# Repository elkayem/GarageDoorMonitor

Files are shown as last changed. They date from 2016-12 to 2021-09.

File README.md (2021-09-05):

# GarageDoorMonitor

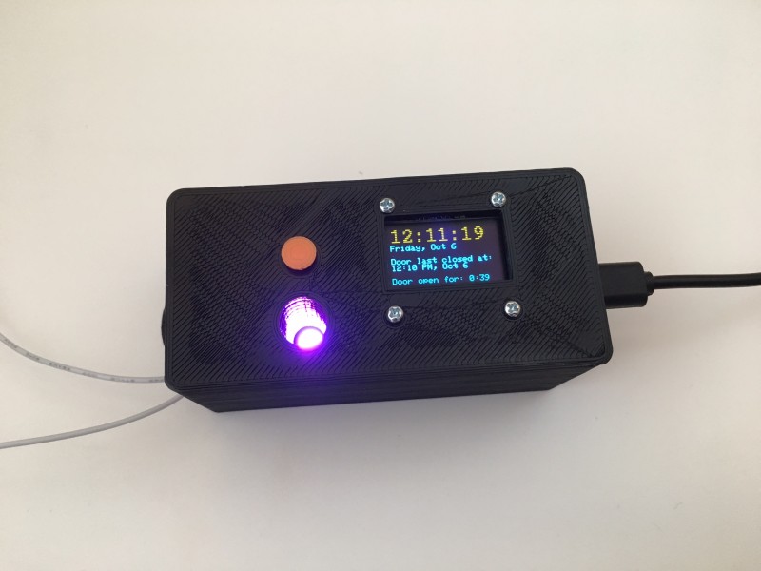
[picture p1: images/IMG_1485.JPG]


The Garage Door Monitor continously monitors whether your garage door is closed, and sends out an email or text message if it has been left open for more than 15 minutes.  It uses the popular ESP8266 WiFi module, and relays messages to you via the IFTTT web service. In our household, we have accidentally left the garage door open on multiple occasions, and this device has saved our bacon more than once.  

Features:
* Email and/or text sent every 15 minutes when your door has been left open, notifying you what time it was opened and how long
* Email/text sent once your door has been closed
* Synchronization with NIST time
* Enable/disable button, which can temporarily disable the monitor
* RGB LED indicating monitor status
* OLED Display
* Configurable settings via WiFi access point
* (Optional) logging of door status via Adafruit IO

The following parts are required, as pictured below:
* NodeMCU V1.0 development board (sometimes also listed as v2 at online shops such as eBay or AliExpress)
* 5V Micro-USB power supply (500 mA or higher)
* Normally Open magnetic switch
* (2) Female headers
* Common Anode RGB LED
* Screw Terminal Block (2 pin 3.5mm Pitch)
* 6x6mm tactile button
* 10K resistor
* (3) 300 Ohm resistors
* (Optional) 4-pin male header
* (Optional) Printed Circuit Board (Eagle files included)
* (Optional) 128x64 I2C OLED Display  (Preferably a two-color display, e.g., yellow/blue)

The PCB is indicated as optional, since the circuit is simple enough to hand solder on a PCB breadboard if desired (schematic shown below).  An OLED display as shown below can enhance the monitor, but is not necessary. There are also two different variations of 3D printed cases provided, one which is used when there is no OLED display, and the other to be used with an OLED.  The non-OLED case was designed in OpenSCAD, and the OLED case (pictured below) was designed in Sketchup 2017.

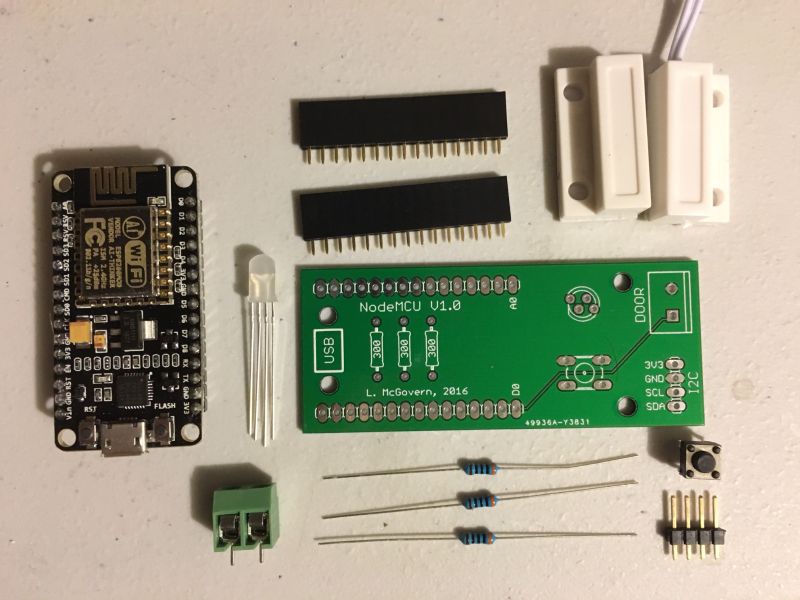
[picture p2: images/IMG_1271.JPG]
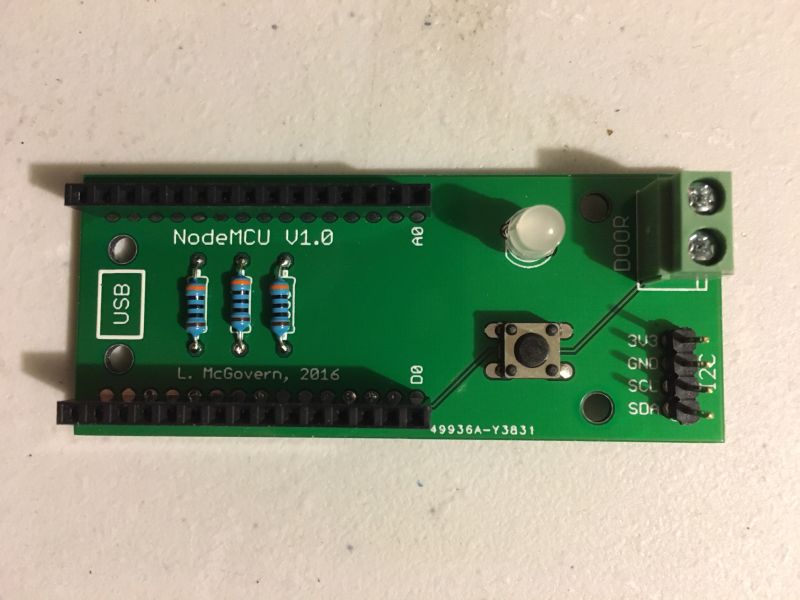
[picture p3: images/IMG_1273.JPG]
 
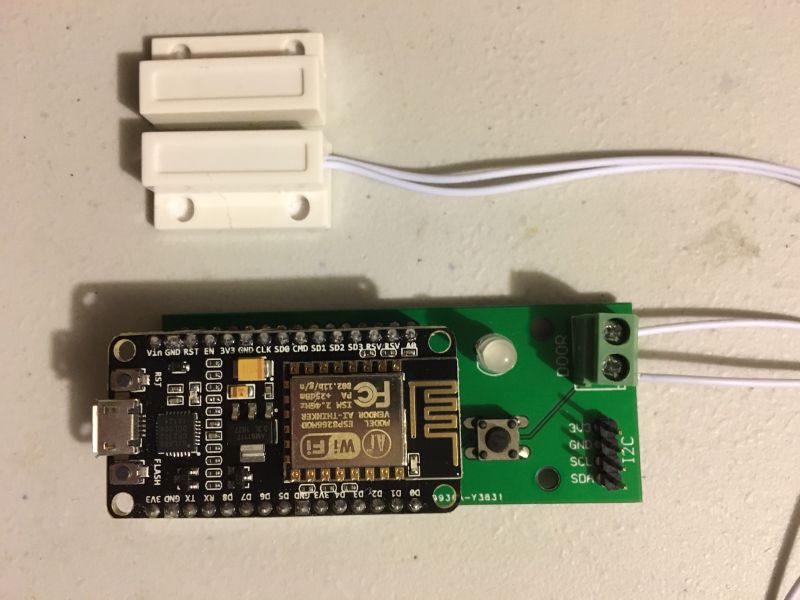
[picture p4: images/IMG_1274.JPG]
MonotorAssembled
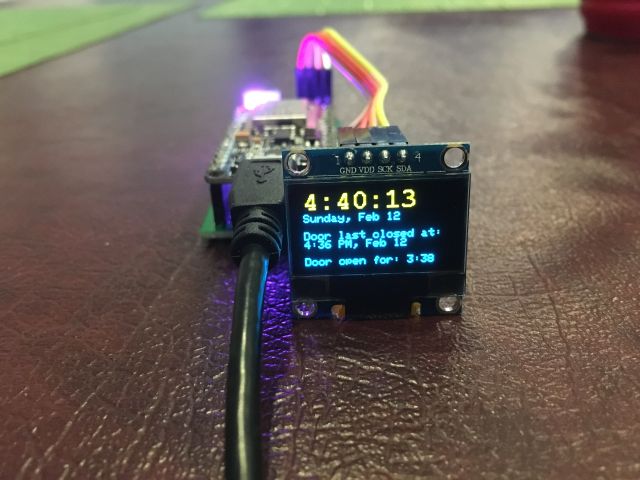
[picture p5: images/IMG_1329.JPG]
OLED
   
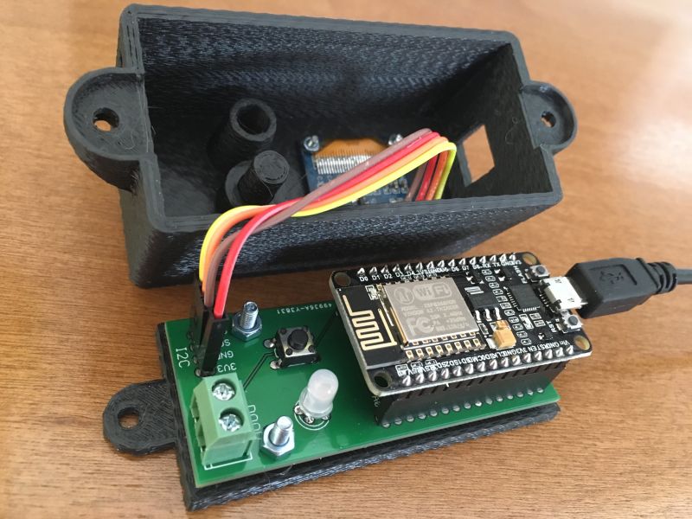
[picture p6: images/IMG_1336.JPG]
OLED_Case
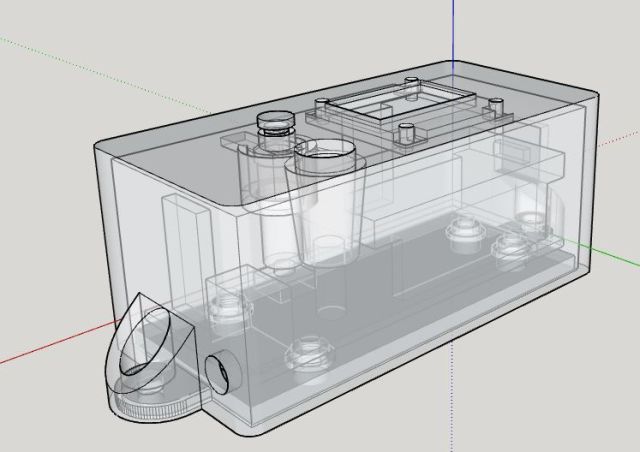
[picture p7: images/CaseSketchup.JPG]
CaseDesign
   
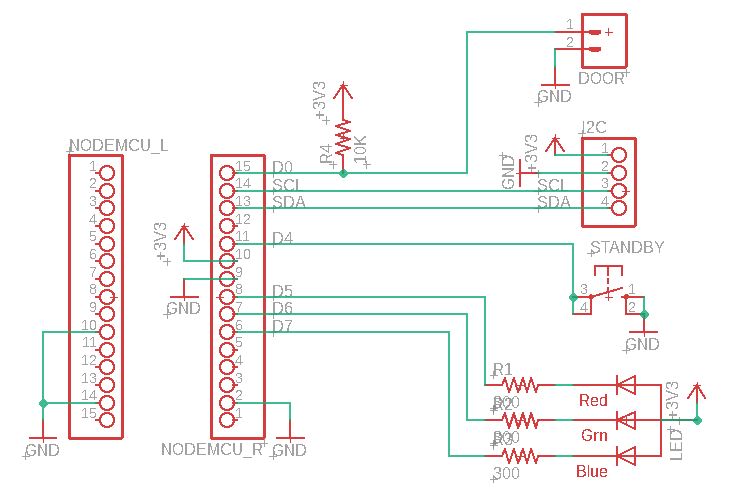
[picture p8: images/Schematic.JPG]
Schematic
 

# Instructions
1. Set up an account at IFTTT.com.  Add the "Webhook" service to your account.  Record the Webhook service API Key for later use, which can be found under the Webhook service settings.  It is a long character sequence following at the end of the URL in Settings, i.e., the character sequence appearing at API_KEY in https://maker.ifttt.com/use/API_KEY.  Note: once the key is created, do not press the "Edit connection" link, or it will create a new key and remove the old one.
2. In IFTTT, create a new applet.  You should see a sentence that says "if +this then that".  Press "+this", and choose the "Webhook" service.  Select the "Receive a web request" trigger.  Call the event "door_open", and create the trigger. Next, press "+that" (from the "if this then that" sentence) and choose the Gmail service.  Select the "Send and email" action.    Choose Gmail as the action (the "then that" part).  Place the desired emails on the To line (text messages can also be sent depending on the provider, e.g., as xxxxxxxxxx@txt.att.net).  Fill out the Subject as: Garage Door Open for  "{{Value1}}" Minutes.  Fill out the body as: The Garage Door was opened at {{Value1}} and has been open for {{Value2}} minutes.  Press the "Create action" buttong.  It should look as shown below:

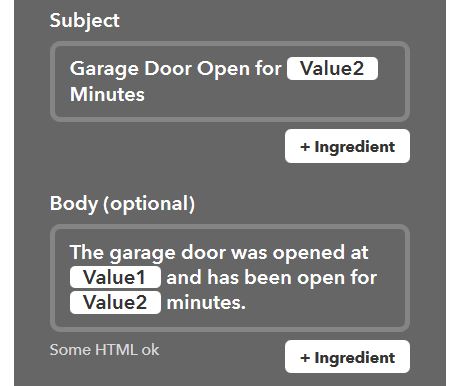
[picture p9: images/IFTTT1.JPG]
door_open
  
  
3. Create another applet in IFTTT with Webhook as the trigger and Gmail as the action.  Call the Webhook event name "door_closed".  Put in the desired email(s) for the Gmail action and fill out the Subject and Body as shown below:

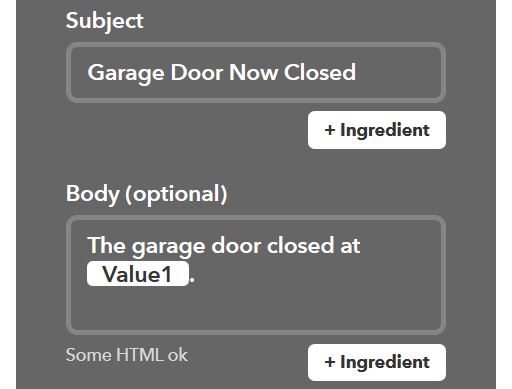
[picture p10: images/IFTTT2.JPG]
door_closed
  
  
4. Create an additional applet which will send out an email at midnight every day giving you confirmation that your door monitor is still working, and the last time the garage door was closed.  This applet also has Webhook as the trigger and Gmail as the action. Call the Webhook event name "door_monitor_active".  Put in the desired email(s) for the Gmail action and fill out the Subject and Body as shown below:

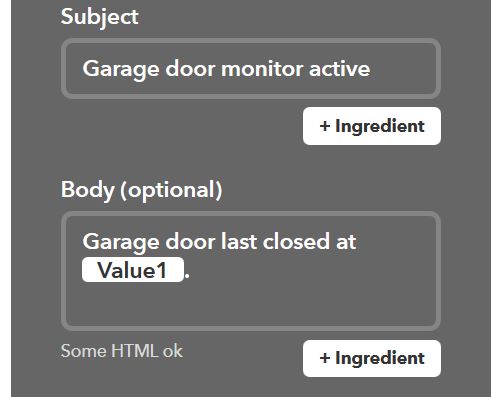
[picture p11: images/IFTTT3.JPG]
door_monitor_active
  
  
5. (Optional) If using Adafruit IO, set up and account at https://io.adafruit.com/.  Record your username and Adafruit IO key for later use.  Add a feed called "garage-door" to your Adafruit IO account.
6. Solder together your garage door monitor, install it in your garage, and plug it in.  If using an OLED display, connect display to the I2C headers using 4" female-female jumper wires, taking special care to match the 3V3 and GND on the display to the board.  Swapping 3V3 and GND will fry your OLED.    
    * **Note #1:** Take care to solder the RGB LED pins in the correct order.  The longest pin is the common anode, which should be soldered in the hole second from the left, where the NodeMCU is on the left side of the board.  The LED case also has a flat edge, which should match the flat edge shown on the board silkscreen.
    * **Note #2:** If you happen to have one of the old PCBs that does not include a 10K resistor on the front of the PCB, you will need to solder a 10K pull-up resistor on the back of the PCB as pictured [here](/images/IMG_2138.JPG).  The PCB pictured on this page above is the old design, with only three resistors on the front, whereas the new PCB has four resistors on the front.  
7. Print out a case on a 3D printer, or design your own.  Two case designs are provided in the "cases" folder. Assemble case and electronics.
8. Flash software to ESP8266 using a micro-USB cable.  This can be done one of two ways: a) Use the compiled .bin files included in the repository, or b) compile and flash the firmware using the Arduino IDE.  I have included two different compiled version.  The file monitor_with_aio.bin should be used if you wish to log the garage door status using Adafruit IO.  The file monitor_without_aio.bin is used if you do not wish to log the status.  Both support the IFTTT web service to email and text message you.  Both also support the OLED screen.  If using one of these files, I recommend using esptool at https://github.com/espressif/esptool to flash the esp8266.  After installing esptool, the following line is used to flash the ESP8266:

    `esptool.py --port COM6 write_flash 0x0000 monitor_without_aio.bin`
  
    where COM6 should be replaced by whatever com port your device is plugged into. (In Windows, this is discoverable using the Device Monitor.) 

    If compiling and flashing using the Arduino IDE, please see the Special Instructions for Compiling and Flashing Firmware Using Arduino IDE at the end of this Readme file.

9. Power garage door monitor using a 5V micro-USB power supply.  When powered for the first time, the monitor will create a WiFi access point called GARAGE_DOOR.  Look for a WiFi network called GARAGE_DOOR on your computer, tablet, or phone and connect to it (default password is PASSWORD, which can be modified in the source code).  (If you don't see one within 30 seconds, it may need to have its settings reset.  Hold down the button for 5 seconds and then cycle the power.)  Your web browser may automatically open up a web page at 192.168.4.1.  If not, connect to this IP address in a browser.  The web page will appear as shown below.  Press "Configure WiFi" and enter in your SSID and password credentials as shown below.  Add the IFTTT API_KEY that you recorded from IFTTT.  Enter in your time zone as indicated, and whether you wish to have the monitor automatically adjust for daylight savings time using US DST rules.  (Enter Y even if it is not currently DST as it will use the date to determine when to adust.) If using the Adafruit IO option, you will also see an entry for Adafruit IO username and key.  Press "save" and the garage door monitor will automatically connect to your WiFi network.

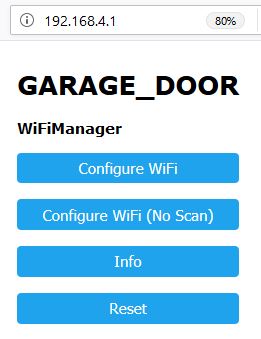
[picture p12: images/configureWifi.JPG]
wifi_accesspoint
   
  
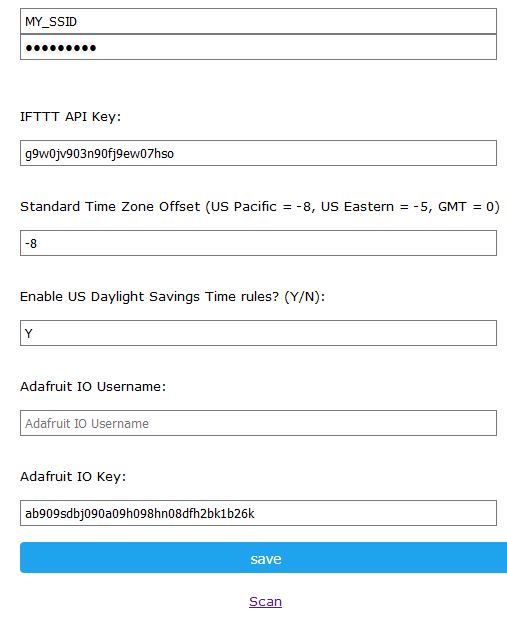
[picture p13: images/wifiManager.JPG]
wifi_manager
  
  
10. Install in your garage and enjoy!  

The LED will be red at turn-on, and will change to green once it has connected to WiFi and synced with NIST time.  When the garage door is shut, the light will remain green.  If open, it will change to magenta for 15 minutes, and will then change to red after it has sent out its first email.  Pressing the tactile button will cause the light to blink blue, and the monitor will not send any emails for 2 hours, or whenever the button is pushed again, which ever comes first.  Any failure to connect to WiFi will cause the monitor to blink red until it is able to reconnect.

The OLED will automatically turn off after five minutes of inactivity while the garage door is closed. This is to prevent OLED burn-in. This time can be extended by changing the OLED_TIMEOUT duration in the code. 

If you ever wish to reset the SSID credentials, IFTTT key, or other settings, press the button for 5 seconds and power cycle.  Follow instructions 

# Special Instructions for Compiling and Flashing Firmware Using Arduino IDE
1. Configure Arduino IDE
  1. Install Arduino IDE 1.8.15 (or later) from arduino.cc
  2. Open File>Preferences, and enter the following URL into "Additional Board Manager URLs": http://arduino.esp8266.com/stable/package_esp8266com_index.json
  3. Open Tools>Board>Board Manager and install the esp8266 boards.  I am currently using v3.0.2, but later versions should also work.
  4. In the Tools menu, configure Board: NodeMCU 1.0 (ESP-12E Module), CPU Frequency: 80 MHz, Upload Speed: 115200.
2. (Optional) If logging is desired, uncomment #define ADAFRUIT_IO and 
3. Install the following libraries.  I have indicated which versions I am currently using, though in most cases later versions should work: NTPClient (3.2.0), WiFi (1.2.7), WiFiManager (2.0.3-alpha), Time (1.6.1), Timezone (1.2.4), ArduinoJson (6.8.3), Adafruit_MQTT (2.4.2), Adafruit_GFX (1.10.10), and Adafruit_SSD1306 (2.4.6).  All of these libraries are added through the Library Manager (Sketch > Include Library > Manage Libraries).
4. If not using an OLED display, you can comment out the line #define OLED_DISPLAY in the sketch.  Otherwise, make sure the libraries Adafruit_GFX and Adafruit_SSD1306 are installed.   
5. Connect the NodeMCU board to your computer using a micro USB cable, and set Tools>Port to the new port that appears.  Your computer should automatically install the driver, but if it does not, you may need to manually download and install the CP2102 driver from http://www.silabs.com/products/mcu/pages/usbtouartbridgevcpdrivers.aspx.  
6. Press the Upload button to compile the sketch and upload to the NodeMCU.  The most common reason for failing to compile are an selecting the wrong board or not installing all the required libraries.

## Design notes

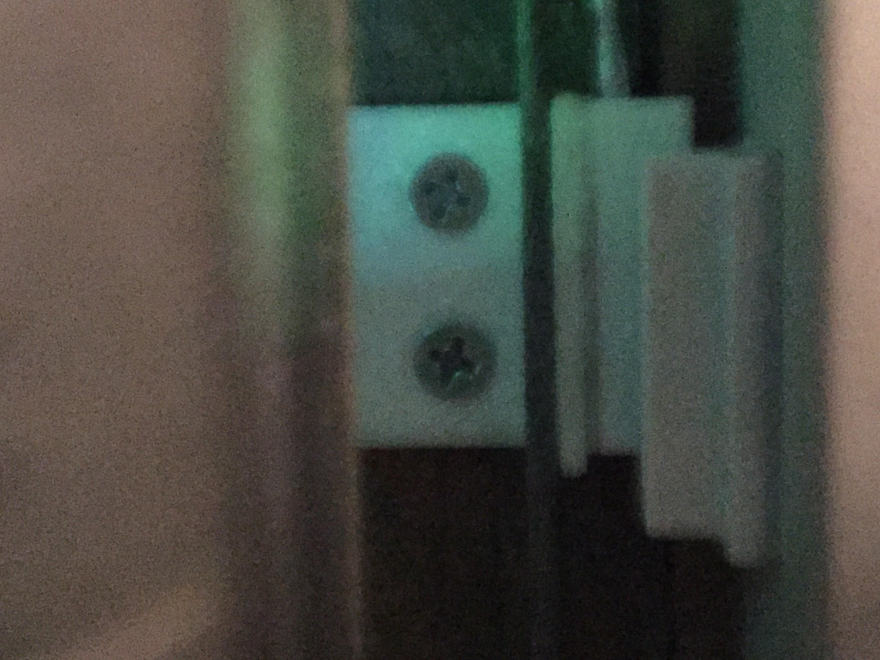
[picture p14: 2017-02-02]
cases/CaseWithoutOLED/Photos/MountedMagnets.jpg

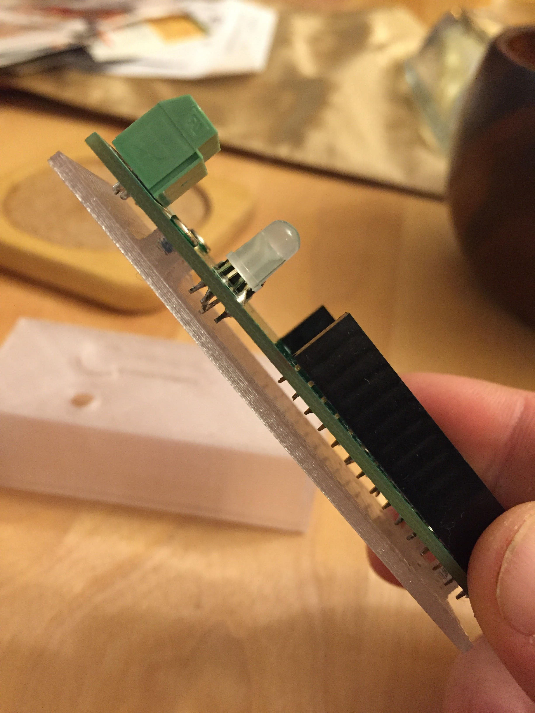
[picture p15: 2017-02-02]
cases/CaseWithoutOLED/Photos/CaseBottomWithStandoffs.jpg

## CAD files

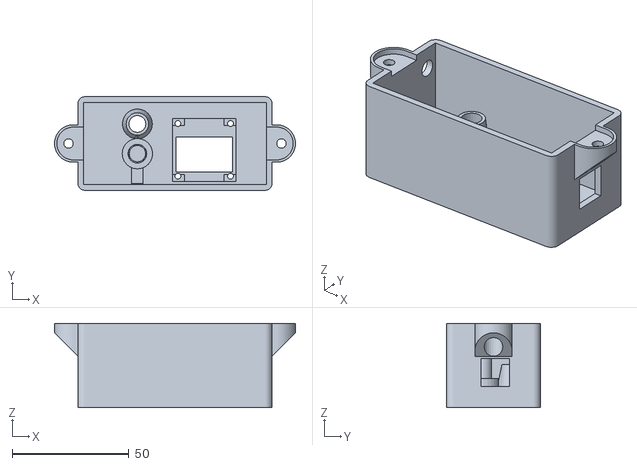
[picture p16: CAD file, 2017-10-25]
cases/CaseWithOLED/GarageDoorMonitorCover.stl
103.0 x 40.0 x 36.1

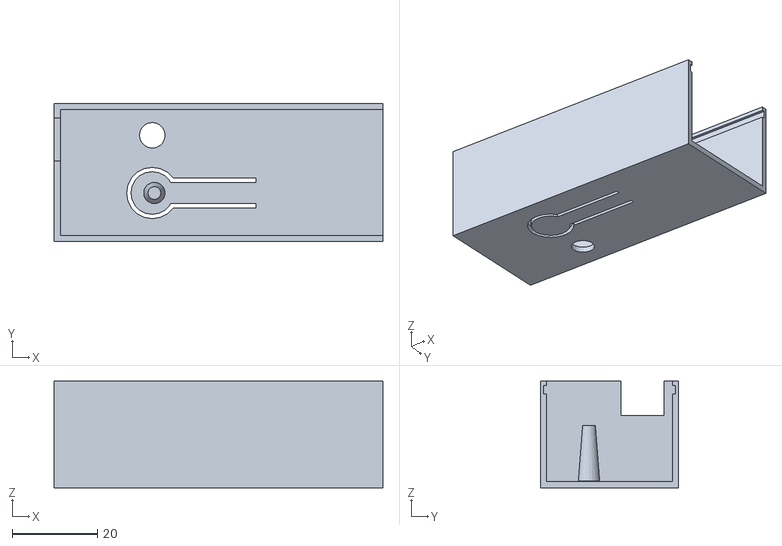
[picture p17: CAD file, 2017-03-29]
cases/CaseWithoutOLED/GarageDoorMonitorCase.stl
77.0 x 32.4 x 25.0

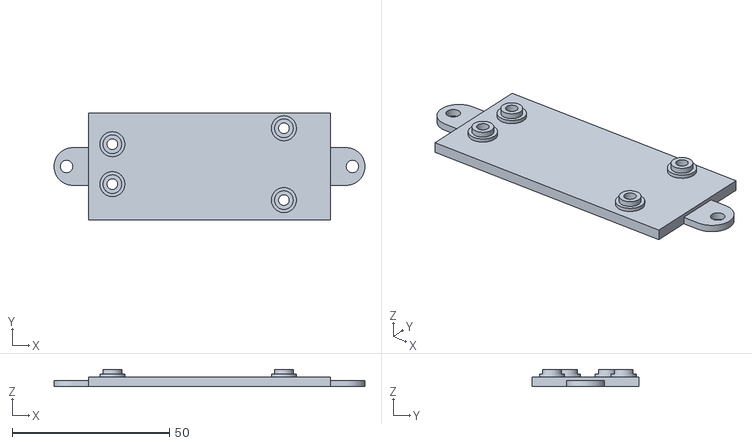
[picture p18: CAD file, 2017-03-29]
cases/CaseWithOLED/GarageDoorMonitorBase.stl
99.0 x 34.0 x 5.50

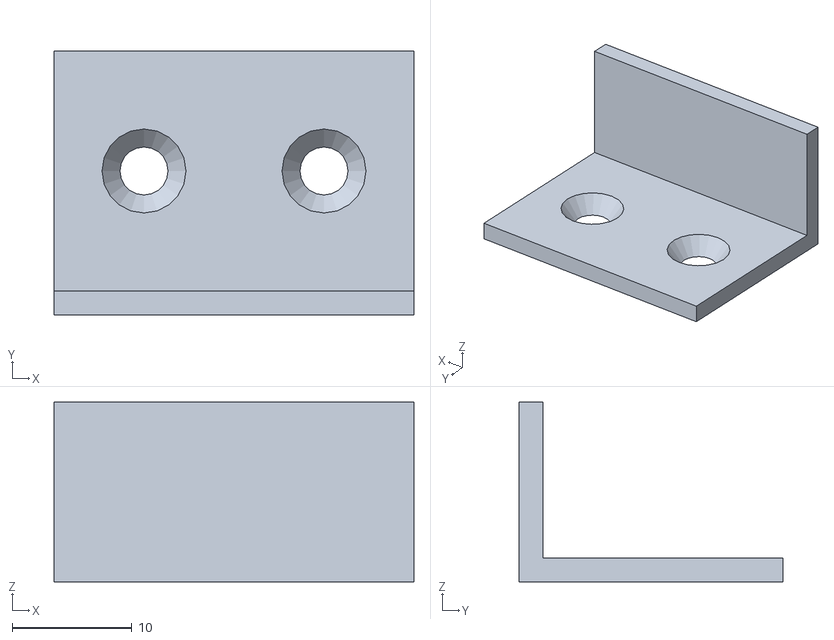
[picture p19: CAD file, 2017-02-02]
cases/CaseWithoutOLED/GargeDoorMonitorMountingPlate.stl
30.0 x 22.0 x 15.0

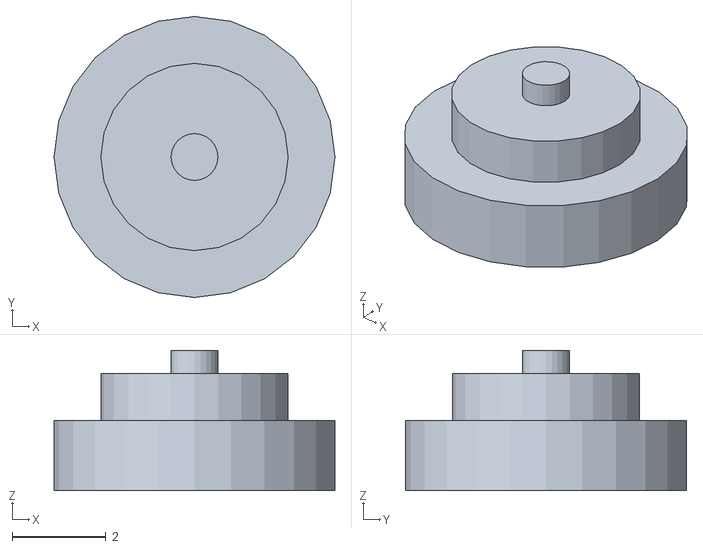
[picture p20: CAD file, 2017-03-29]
cases/CaseWithOLED/Button.stl
6.00 x 6.00 x 3.00

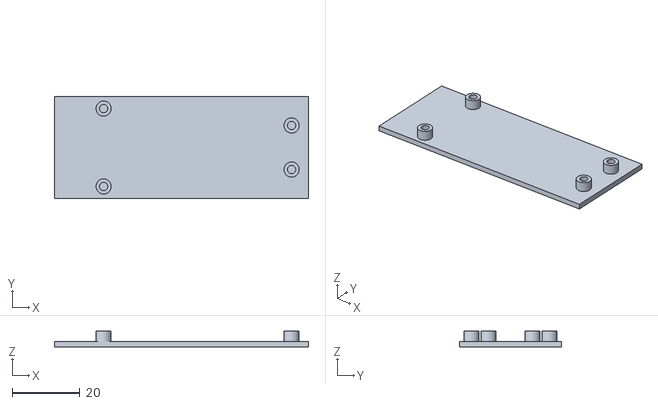
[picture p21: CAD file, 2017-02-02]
cases/CaseWithoutOLED/GarageDoorMonitorBottom.stl
75.0 x 30.0 x 4.60

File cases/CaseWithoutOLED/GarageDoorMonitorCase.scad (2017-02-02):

boardWidth = 30;
boardLength = 75;
boardThickness = 1.6;
wallThickness = 1.5;
gap = .5;
caseHeight = 25;
caseLength = boardLength+wallThickness+gap;
caseWidth = boardWidth+2*wallThickness-2*gap+.4;
buttonRad = 5;
cutWidth = 1;

// The standoffs are sized for tiny screws I pulled out of an old laptop.
// Printed on a 0.5 mm nozzle, so if using a smaller nozzle may want to
// shrink the boardScrewDiam a tad.

boardHole1PosX = 14.5;
boardHole1PosY = 3.5;
boardHole2PosX = boardLength-5;
boardHole2PosY = 8.5;
boardScrewDiam = 2.5;
standoffHeight = 3;
slop = 0.4;

caseTop();

translate([0,50,0])
caseBottom();

module caseBottom() 
{
    cube([boardLength,boardWidth,boardThickness]);
    translate([boardHole1PosX,boardHole1PosY,boardThickness])
    difference()
    {
        cylinder(d=boardScrewDiam+2,h=standoffHeight,$fn=20);
        cylinder(d=boardScrewDiam,h=standoffHeight,$fn=20);
    }
    translate([boardHole1PosX,boardWidth-boardHole1PosY,boardThickness])
    difference()
    {
        cylinder(d=boardScrewDiam+2,h=standoffHeight,$fn=20);
        cylinder(d=boardScrewDiam,h=standoffHeight,$fn=20);
    }    translate([boardHole2PosX,boardHole2PosY,boardThickness])
    difference()
    {
        cylinder(d=boardScrewDiam+2,h=standoffHeight,$fn=20);
        cylinder(d=boardScrewDiam,h=standoffHeight,$fn=20);
    }
    translate([boardHole2PosX,boardWidth-boardHole2PosY,boardThickness])
    difference()
    {
        cylinder(d=boardScrewDiam+2,h=standoffHeight,$fn=20);
        cylinder(d=boardScrewDiam,h=standoffHeight,$fn=20);
    }

}
module caseTop()
{
difference()
{
    cube([caseLength,caseWidth,caseHeight]);
    // carve out general insides
    translate([wallThickness,wallThickness,wallThickness])
    cube([caseLength-wallThickness,caseWidth-2*wallThickness,caseHeight]);
    // carve out slots for board
    translate([wallThickness,0.5*(caseWidth-boardWidth)-slop,caseHeight-3])
    cube([caseLength,boardWidth+2*slop,boardThickness+slop]);
    // carve out sensor wire slot
    translate([0,caseWidth-12-wallThickness,caseHeight-8])
    cube([wallThickness,10,8+boardThickness]);   
    // carve out button press 
    translate([22+1,caseWidth-21,0])
    {
        difference()
        {
            cylinder(r=buttonRad+cutWidth,h=boardThickness,$fn=20);
            cylinder(r=buttonRad, h=boardThickness,$fn=20);
            translate([0,-.5*buttonRad,0])
            cube([2*buttonRad,buttonRad,boardThickness]);
        }
        
        translate([sqrt(3)/2*buttonRad,-0.5*buttonRad-cutWidth,0])
        cube([20,cutWidth,boardThickness]);
        translate([sqrt(3)/2*buttonRad,0.5*buttonRad,0])
        cube([20,cutWidth,boardThickness]);
    }
    
    // carve out LED view hole
    
    translate([22+1,caseWidth-6-wallThickness,0])
    cylinder(r=3,h=boardThickness,$fn=20);
}

translate([wallThickness+22,caseWidth-21,boardThickness])
cylinder(d1=5,d2=3,h=caseHeight-12,$fn=20);
}

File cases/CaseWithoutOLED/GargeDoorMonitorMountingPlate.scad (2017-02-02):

magnetLength = 30;
magnetWidth = 15;
thickness = 2;
flangeWidth = 20;
screwOD = 7;
screwID = 4;
$fn=20;

difference()
{
    cube([magnetLength,flangeWidth,thickness]);
    translate([0,flangeWidth/2,0])
    {
        translate([magnetLength/4,0,0])
        cylinder(d1=screwID,d2=screwOD,thickness);
        translate([3*magnetLength/4,0,0])
        cylinder(d1=screwID,d2=screwOD,thickness);
    }
}
translate([0,-thickness,0])
cube([magnetLength,thickness,magnetWidth]);

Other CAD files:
cases/CaseWithOLED/GarageDoorMonitorCaseWithOLED.skp

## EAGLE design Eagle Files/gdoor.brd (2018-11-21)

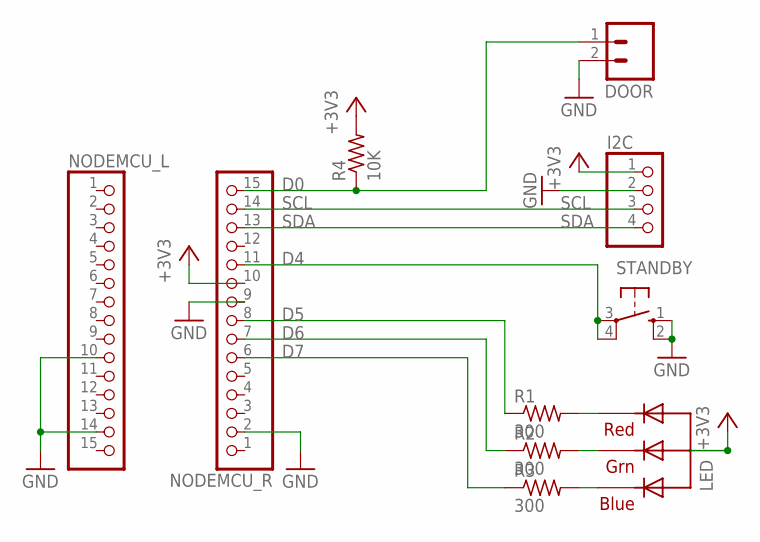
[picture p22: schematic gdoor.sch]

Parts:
DOOR: M025MM; SCREWTERMINAL-5MM-2
I2C: PINHD-1X4; 1X04
LED: RGBLED_CA-5MM; LED5MMRGB
NODEMCU_L: PINHD-1X15; 1X15
NODEMCU_R: PINHD-1X15; 1X15
R1, R2, R3: 300; 0207/10
R4: 10K; 0207/10
STANDBY: 10-XX; B3F-10XX

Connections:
+3V3: I2C.1, LED.2 (VCC), NODEMCU_R.10, R4.2
BLUE: LED.4 (BLUE), R3.2
D0: DOOR.1, NODEMCU_R.15, R4.1
D4: NODEMCU_R.11, STANDBY.3, STANDBY.4 (P1)
D5: NODEMCU_R.8, R1.1
D6: NODEMCU_R.7, R2.1
D7: NODEMCU_R.6, R3.1
GND: DOOR.2, I2C.2, NODEMCU_L.10, NODEMCU_L.14, NODEMCU_R.2, NODEMCU_R.9, STANDBY.1 (S), STANDBY.2 (S1)
GRN: LED.3 (GREEN), R2.2
RED: LED.1 (RED), R1.2
SCL: I2C.3, NODEMCU_R.14
SDA: I2C.4, NODEMCU_R.13

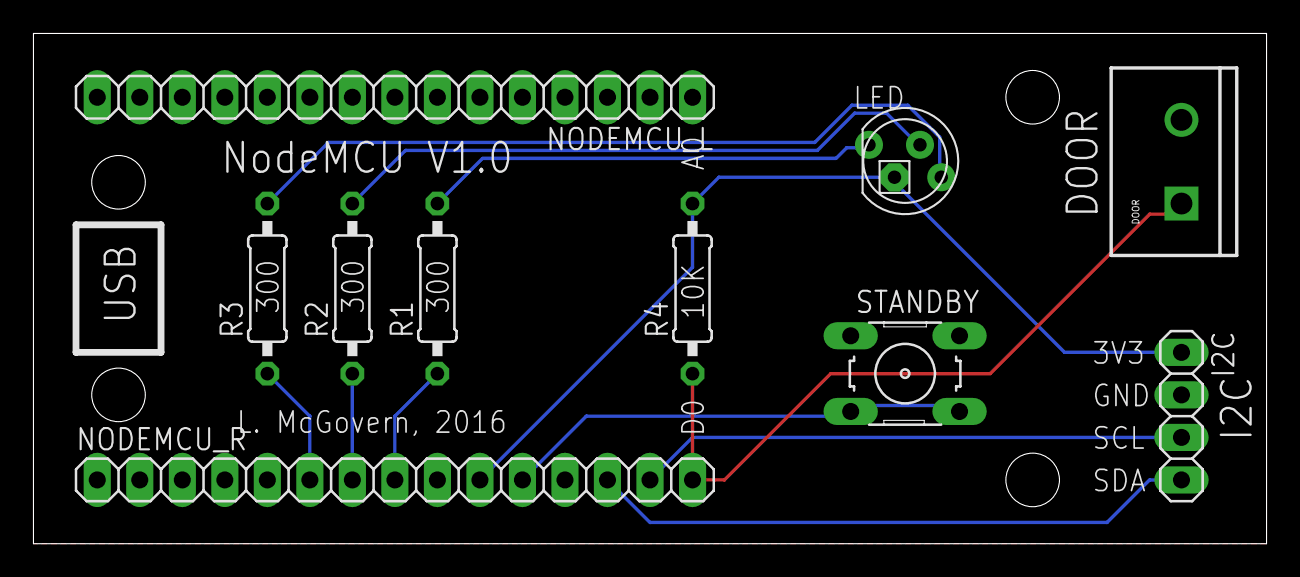
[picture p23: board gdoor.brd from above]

Board: 2 copper layers, 73.7 x 30.5 mm, 10 parts (0 on the bottom side), 12 nets.

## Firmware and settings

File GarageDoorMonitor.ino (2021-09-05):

/*    
 *    GarageDoorMonitor
 *	  Copyright (C) 2021  Larry McGovern
 *	
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
 *    This program is distributed in the hope that it will be useful,
 *    but WITHOUT ANY WARRANTY; without even the implied warranty of
 *    MERCHANTABILITY or FITNESS FOR A PARTICULAR PURPOSE.  See the
 *    GNU General Public License <http://www.gnu.org/licenses/> for more details.
 */

//#define ADAFRUIT_IO  // Uncomment if using Adafruit IO account
#define OLED_DISPLAY // Comment out if not using an OLED Display

#include <NTPClient.h>
#include <ESP8266WiFi.h>
#include <WiFiUdp.h>
#include <WiFiManager.h>
#include <TimeLib.h>
#include <Timezone.h>
#include <ArduinoJson.h>
#include <EEPROM.h>

#ifdef OLED_DISPLAY
#include <Adafruit_GFX.h>
#include <Adafruit_SSD1306.h>
#include <Fonts/FreeMonoBold12pt7b.h>
#endif

#ifdef ADAFRUIT_IO
#include "Adafruit_MQTT.h"
#include "Adafruit_MQTT_Client.h"
#endif

#define D0 16 // LED_BUILTIN
#define D1 5 // I2C Bus SCL (clock)
#define D2 4 // I2C Bus SDA (data)
#define D3 0 // 
#define D4 2 //  Blue LED 
#define D5 14 // SPI Bus SCK (clock)
#define D6 12 // SPI Bus MISO 
#define D7 13 // SPI Bus MOSI
#define D8 15 // SPI Bus SS (CS) 
#define D9 3 // RX0 (Serial console) 
#define D10 1 // TX0 (Serial console) 

#define OPEN HIGH  //  For normally open read switch, OPEN = HIGH.  Swap if using normally closed switch
#define CLOSED LOW

// Timezone and DST EEPROM addresses
char tz_str[4], dst_str[2];
#define TZ_ADDR  0
#define TZ_LENGTH 4
#define DST_ADDR 4
#define DST_LENGTH 2

// IFTTT
const char* host = "maker.ifttt.com";
#define API_KEY_LENGTH 50
#define API_KEY_ADDR TZ_LENGTH + DST_LENGTH  // First six bytes store time zone info
char apiKey[API_KEY_LENGTH];

#ifdef ADAFRUIT_IO  // **** Adafruit IO Setup ****//
  #define AIO_SERVER      "io.adafruit.com"
  #define AIO_SERVERPORT  1883
  #define AIO_USERNAME_LENGTH 50
  #define AIO_KEY_LENGTH 50
  #define AIO_USERNAME_ADDR API_KEY_ADDR + API_KEY_LENGTH
  #define AIO_KEY_ADDR AIO_USERNAME_ADDR + AIO_USERNAME_LENGTH

  char aioUsername[AIO_USERNAME_LENGTH], aioKey[AIO_KEY_LENGTH], aioFeed[AIO_USERNAME_LENGTH+20];  

  // Setup the MQTT client class by passing in the WiFi client and MQTT server and login details.
  WiFiClient mqtt_client;
  Adafruit_MQTT_Client mqtt(&mqtt_client, AIO_SERVER, AIO_SERVERPORT, aioUsername, aioKey);

  // Setup garage door feed
  Adafruit_MQTT_Publish garage_door = Adafruit_MQTT_Publish(&mqtt, aioUsername);
  
  #define EEPROM_LENGTH TZ_LENGTH + DST_LENGTH + API_KEY_LENGTH + AIO_USERNAME_LENGTH + AIO_KEY_LENGTH
#else
  #define EEPROM_LENGTH TZ_LENGTH + DST_LENGTH + API_KEY_LENGTH
#endif

const char* month_names[] = {"Jan", "Feb", "Mar", "Apr", "May", "June", "July", "Aug", "Sept", "Oct", "Nov", "Dec"};
const char* day_names[] = {"Sunday", "Monday", "Tuesday", "Wednesday", "Thursday", "Friday", "Saturday"};
const char* am_pm[] = {"AM", "PM"};
const char* door_open_closed[] = {"Door closed", "Door open"};

// US Pacific Time Zone -- Time zone is configurable in EEPROM
TimeChangeRule myDST = {"PDT", Second, Sun, Mar, 2, -420};    //Daylight time = UTC - 7 hours
TimeChangeRule mySTD = {"PST", First, Sun, Nov, 2, -480};     //Standard time = UTC - 8 hours
Timezone myTZ(myDST, mySTD);

WiFiUDP ntpUDP;
NTPClient timeClient(ntpUDP, "time.nist.gov", 0, 7200000); // Update time every two hours

int wifiStatus, doorStatus, doorStatusPrev = CLOSED, openMessage = false;
unsigned long int changeTime, changeTimer, lastCheckTime, standbyModeTime, resetTimer, oledTimer;
char changeTimeStr[50], closeTimeStr[20];
int dailyMessageSent;
int prevSecond;

bool redState, greenState, blueState, blinkState, standbyMode = 0;

#define DOOR       D0
#define STANDBY    D4
#define RED_LED    D5
#define GREEN_LED  D6
#define BLUE_LED   D7

#define TIMER_MS 900000 // Time to send out alert, in ms.  900000 = 15 minutes
#define BLINK_PERIOD 500
#define DOOR_CHECK_PERIOD 100   // Check door status every 100 msec
#define STANDBY_TIMEOUT 7200000  // Automatically go out of standby mode after 2 hours
#define WIFI_RESET_TIMEOUT 1800000 // Reboot if wifi drops out for more than 30 minutes
#define OLED_TIMEOUT 300000 // Turn OLED off wheen door closed and after 5 minutes of inactivity 

#ifdef OLED_DISPLAY
  #define SCREEN_WIDTH 128 // OLED display width, in pixels
  #define SCREEN_HEIGHT 64 // OLED display height, in pixels
  #define OLED_RESET  D8
  Adafruit_SSD1306 display(SCREEN_WIDTH, SCREEN_HEIGHT, &Wire, OLED_RESET);
#endif

void setup() {
  int i;
  
  Serial.begin(115200);

  pinMode(STANDBY, INPUT_PULLUP);
  pinMode(DOOR, INPUT);  // GPIO16 does not have a pull-up resistor, must be added externally
  pinMode(RED_LED, OUTPUT);
  pinMode(GREEN_LED, OUTPUT);
  pinMode(BLUE_LED, OUTPUT);
  
#ifdef OLED_DISPLAY
  display.begin(SSD1306_SWITCHCAPVCC, 0x3C);  // OLED I2C Address, may need to change for different device,
                                              // Check with I2C_Scanner
  display.setTextSize(1);
  display.setTextColor(WHITE);
  display.clearDisplay();
  display.setCursor(0,0);
  display.println("Connecting...");
  display.display();
#endif
  
  status_leds(1, 0, 0, 0); // Solid red at turn-on

  
  EEPROM.begin(EEPROM_LENGTH);

  // Read info from EEPROM
  eepromRead(tz_str, TZ_ADDR, TZ_LENGTH);
  eepromRead(dst_str, DST_ADDR, DST_LENGTH);
  eepromRead(apiKey, API_KEY_ADDR, API_KEY_LENGTH);
  
  #ifdef ADAFRUIT_IO
    eepromRead(aioUsername, AIO_USERNAME_ADDR, AIO_USERNAME_LENGTH);
    eepromRead(aioKey, AIO_KEY_ADDR, AIO_KEY_LENGTH);
  #endif
    
  // Setup WiFiManager

  WiFiManager MyWifiManager;

  MyWifiManager.setAPCallback(configModeCallback);
  
  WiFiManagerParameter custom_api_text("<br/><br/><br/>IFTTT API Key:<br/>");
  MyWifiManager.addParameter(&custom_api_text);
  
  WiFiManagerParameter custom_api_key("apikey", "API Key", apiKey, API_KEY_LENGTH);
  MyWifiManager.addParameter(&custom_api_key);

  WiFiManagerParameter custom_timezone_text("<br/><br/><br/>Standard Time Zone Offset (US Pacific = -8, US Eastern = -5, GMT = 0) :<br/>");
  MyWifiManager.addParameter(&custom_timezone_text);
  
  WiFiManagerParameter custom_timezone("timezone", "Time Zone", tz_str, TZ_LENGTH);
  MyWifiManager.addParameter(&custom_timezone);

  WiFiManagerParameter custom_dst_text("<br/><br/><br/>Enable US Daylight Savings Time rules? (Y/N):<br/>");
  MyWifiManager.addParameter(&custom_dst_text);
  
  WiFiManagerParameter custom_dst("dst", "DST", dst_str, DST_LENGTH);
  MyWifiManager.addParameter(&custom_dst);

  #ifdef ADAFRUIT_IO
    WiFiManagerParameter custom_aio_username_text("<br/><br/><br/>Adafruit IO Username:<br/>");
    MyWifiManager.addParameter(&custom_aio_username_text);
  
    WiFiManagerParameter custom_aio_username("aio_username", "Adafruit IO Username", aioUsername, AIO_USERNAME_LENGTH);
    MyWifiManager.addParameter(&custom_aio_username);

    WiFiManagerParameter custom_aio_key_text("<br/><br/><br/>Adafruit IO Key:<br/>");
    MyWifiManager.addParameter(&custom_aio_key_text);
  
    WiFiManagerParameter custom_aio_key("aio_key", "Adafruit IO Key", aioKey, AIO_KEY_LENGTH);
    MyWifiManager.addParameter(&custom_aio_key);
  #endif

  MyWifiManager.setTimeout(900);  // Timeout after 15 minutes
  if(!MyWifiManager.autoConnect("GARAGE_DOOR","PASSWORD")) {
    delay(3000);
    ESP.restart();  // Reboot if timeout
    delay(5000);
  }


  bool saveEEPROM = false;
  if (strcmp(apiKey, custom_api_key.getValue()) || strcmp(tz_str, custom_timezone.getValue()) || strcmp(dst_str, custom_dst.getValue())) {  // If data changed, need to save to EEPROM
    saveEEPROM = true;
  }
  #ifdef ADAFRUIT_IO
    if (strcmp(aioKey, custom_aio_key.getValue()) || strcmp(aioUsername, custom_aio_username.getValue())) {  
      saveEEPROM = true;
    }  
  #endif

  if (saveEEPROM) {
    strcpy(tz_str, custom_timezone.getValue());
    for (i=0; i<TZ_LENGTH; i++) {
      EEPROM.write(TZ_ADDR+i, tz_str[i]);
    }
    
    strcpy(dst_str, custom_dst.getValue());
    for (i=0; i<DST_LENGTH; i++) {
      EEPROM.write(DST_ADDR+i, dst_str[i]);
    }
    
    strcpy(apiKey, custom_api_key.getValue());
    for (i=0; i<API_KEY_LENGTH; i++) {
      EEPROM.write(API_KEY_ADDR+i, apiKey[i]);
    }
    
    #ifdef ADAFRUIT_IO
      strcpy(aioUsername, custom_aio_username.getValue());
      for (i=0; i<AIO_USERNAME_LENGTH; i++) {
        EEPROM.write(AIO_USERNAME_ADDR+i, aioUsername[i]);
      }  
      
      strcpy(aioKey, custom_aio_key.getValue());
      for (i=0; i<AIO_KEY_LENGTH; i++) {
        EEPROM.write(AIO_KEY_ADDR+i, aioKey[i]);
      }   
    #endif
    
    EEPROM.commit();
  }

  // Update timezone info
  int tz = atoi(tz_str);
  if (tz < -24 || tz > 24) tz = 0; 
  mySTD.offset = tz*60;

  if (dst_str[0] == 'y' || dst_str[0] == 'Y') {
    myDST.offset = mySTD.offset + 60;
    switch (tz) {
      case -8:
        strcpy(mySTD.abbrev, "PST");
        strcpy(myDST.abbrev, "PDT");
        break;
      case -7:
        strcpy(mySTD.abbrev, "MST");
        strcpy(myDST.abbrev, "MDT");
        break;        
      case -6:
        strcpy(mySTD.abbrev, "CST");
        strcpy(myDST.abbrev, "CDT");
        break; 
      case -5:
        strcpy(mySTD.abbrev, "EST");
        strcpy(myDST.abbrev, "EDT");
        break;    
      default:   
        strcpy(mySTD.abbrev, "STD");
        strcpy(myDST.abbrev, "DST");  
    }
  }
  else {
    myDST.offset = mySTD.offset;
      strcpy(mySTD.abbrev, "");
      strcpy(myDST.abbrev, "");
  }
  myTZ = Timezone(myDST, mySTD);

#ifdef ADAFRUIT_IO
  mqtt = Adafruit_MQTT_Client(&mqtt_client, AIO_SERVER, AIO_SERVERPORT, aioUsername, aioKey);
  strcpy(aioFeed,aioUsername); // Add feed
  strcat(aioFeed, "/feeds/garage-door"); // Add feed
  garage_door = Adafruit_MQTT_Publish(&mqtt, aioFeed);
#endif
    
  wifiStatus = 1;
  Serial.println(" Connected");

#ifdef OLED_DISPLAY  
  display.clearDisplay();
  display.setCursor(0,0);
  display.print("Wifi Connected");
  display.setCursor(0,28);
  display.println("Updating local time");
  display.display();
#endif

  timeClient.begin();
  while (!timeClient.update()) {
    delay(500);
    Serial.print(".");
  }
  Serial.println(" Local time updated.");

  changeTime = millis();
  changeTimer = changeTime;
  lastCheckTime = millis() - DOOR_CHECK_PERIOD;
  standbyModeTime = millis();
  oledTimer = millis();
  updateTime(1);
  dailyMessageSent = day();
  
  status_leds(0, 1, 0, 0); // Set-up complete, set to green
}

void loop()
{
  if (second() != prevSecond) {
    updateTime(0);  // Update time displayed on OLED
    prevSecond = second();
  }
  blink_leds();
  readStandbyButton();

  if (!wifiStatus) {
    if (millis() - resetTimer > WIFI_RESET_TIMEOUT) {
       delay(3000);
       ESP.restart();  // Reboot if timeout
       delay(5000);
    }
  }
  else resetTimer = millis();

  if (millis() - lastCheckTime < DOOR_CHECK_PERIOD) return; 
  
  doorStatus = digitalRead(DOOR);
  
  if (doorStatus != doorStatusPrev) { // Door has opened or closed
    
    delay(500);  doorStatus = digitalRead(DOOR);  // Resample after 500 msec, to filter out glitches

    if (doorStatus == doorStatusPrev) return;     // Return if change in status was a glitch
    
    if (!blinkState) { // Change LED to indicate door open/shut only if LED not blinking
      if (doorStatus == CLOSED)
        status_leds(0, 1, 0, 0); // Door shut, status = Green
      else
        status_leds(1, 0, 1, 0); // Door open, status = Magenta
    } 

    changeTime = millis();
    changeTimer = changeTime;
    oledTimer = changeTime;
    updateTime(1);
    Serial.println(String(door_open_closed[(int)(doorStatus==OPEN)]) + " at " + changeTimeStr);
    sendAdaIO();
    doorStatusPrev = doorStatus;   
  }

  if ((doorStatus == OPEN) || standbyMode) oledTimer = millis(); // OLED timer runs only wheen door is closed and not in standby mode
  
  if (standbyMode) {
    if (millis() - standbyModeTime > STANDBY_TIMEOUT) {
      standbyMode = 0;  // Automatically go out of standby mode after timeout period
      if (doorStatus == CLOSED)
        status_leds(0, 1, 0, 0); // Door shut, status = Green
      else {
        changeTimer = millis();  // Reset change timer
        status_leds(1, 0, 1, 0); // Door open, status = Magenta
      }
    } 
    else
      return;
  }
  
  if ( (doorStatus == OPEN) && (millis() - changeTimer > TIMER_MS)) { // Door has been open for at least 15 minutes
    if (!sendIFTTT("/trigger/door_open/with/key/")) return; // Send door open message, return if failed
    changeTimer = millis();
    openMessage = true;
    status_leds(1, 0, 0, 0); // Turn LED red if door open for > 15 min
  }
  else if ( (openMessage == true) && (doorStatus == CLOSED)) { // Open door message has gone out, but door is closed now
    if (!sendIFTTT("/trigger/door_closed/with/key/")) return;  // Send door closed message, return if failed
    openMessage = false;
    status_leds(0, 1, 0, 0); // Turn LED green once door has closed again
  }
  else if (day() != dailyMessageSent) { // It's a new day
    if (!sendIFTTT("/trigger/door_monitor_active/with/key/")) return;  // Send an "I'm Healthy" message, return if failed
    dailyMessageSent = day();
    status_leds(0, 1, 0, 0); // Turn green, system is healthy
  }
  
  lastCheckTime = millis();
}

#define colonDigit(digit) digit < 10 ? ":0" : ":"

void updateTime(int updateChangeTime) {  // If updateChangeTime == 1, the global changeTimeString is updated
  char tod_hm[10],tod_hms[15], date_str[25], Timer[10];
  int timerMin, timerSec;
  TimeChangeRule *tcr;

  timeClient.update();

  setTime(myTZ.toLocal(timeClient.getEpochTime(), &tcr));

  sprintf(tod_hm, "%d%s%d", hourFormat12(), colonDigit(minute()), minute());  // Hours, minutes
  sprintf(tod_hms, "%s%s%d", tod_hm, colonDigit(second()), second());  // Hours, minutes, seconds

  if (updateChangeTime) {  
    sprintf(changeTimeStr, "%s %s %s on %s, %s %d, %d", tod_hm,  am_pm[isPM()],
          tcr -> abbrev, day_names[weekday() - 1], month_names[month() - 1], day(), year());
    if (doorStatus == CLOSED) {
      sprintf(closeTimeStr, "%s %s, %s %d", tod_hm,  am_pm[isPM()], month_names[month() - 1], day());  
    }
  }

#ifdef OLED_DISPLAY
  sprintf(date_str, "%s, %s %d", day_names[weekday() - 1], month_names[month() - 1], day());
  display.clearDisplay();

  if ((millis() - oledTimer) < OLED_TIMEOUT) {
    display.setCursor(0,8);
    display.setFont(&FreeMonoBold12pt7b);
    display.println(tod_hms);
    display.setCursor(0,23);
    display.setFont(); 
    display.println(date_str);
    display.println("");
    display.println("Door last closed at:"); 
    display.println(closeTimeStr);
  }

  if (!wifiStatus) {
    display.println("Error: No Internet");
  }
  else if (standbyMode) {
    timerSec = (STANDBY_TIMEOUT - (millis() - standbyModeTime)) / 1000;
    timerMin = timerSec / 60;
    timerSec -= 60*timerMin;    
    sprintf(Timer,"%d%s%d",timerMin,colonDigit(timerSec),timerSec);
    display.println("");
    display.print("Standby Mode: ");
    display.print(Timer); 
  }
  else if (doorStatus == OPEN) {
    timerSec = (millis() - changeTime) / 1000;
    timerMin = timerSec / 60;
    timerSec -= 60*timerMin;
    sprintf(Timer,"%d%s%d",timerMin,colonDigit(timerSec),timerSec);
    display.println("");
    display.print("Door open for: ");
    display.print(Timer); 
  }
  display.display();
#endif
}


int sendAdaIO()
{
#ifdef ADAFRUIT_IO
  if (!mqtt.connected()) {  // Reconnect if not connected
     Serial.print("Connecting to MQTT... ");

     uint8_t retries = 3;
     int8_t ret;
     while ((ret = mqtt.connect()) != 0) { // Try to connect three times
       Serial.println(mqtt.connectErrorString(ret));
       Serial.println("Retrying MQTT connection in 5 seconds...");
       mqtt.disconnect();
       delay(1000);  // wait 1 second1
       retries--;
       if (retries == 0) {
         return(0);
       }
    }
    Serial.println("MQTT Connected!");
  }
  
  Serial.println("Sending to Adafruit.io");

  garage_door.publish(doorStatus==CLOSED);  // Previous door state
  delay(1000);
  garage_door.publish(doorStatus==OPEN);    // Current door state

  Serial.println("Sent");
#endif
  return(1);
}
  
int sendIFTTT(String url)
{
  static int ifttt_retry = 0;
  
  Serial.print("connecting to ");
  Serial.println(host);
  char buffer[256];

  WiFiClient client;
  const int httpPort = 80;
  if (!client.connect(host, httpPort)) {
    Serial.println("connection failed");
    status_leds(1, 0, 0, 1); // Blink red, unable to connect to IFTTT
    wifiStatus = 0;
    return (0);
  }
  wifiStatus = 1;

  StaticJsonDocument<200> jsonDoc;

  jsonDoc["value1"] = changeTimeStr;
  jsonDoc["value2"] = (millis() - changeTime) / 60000;
  
  serializeJson(jsonDoc, buffer, sizeof(buffer));
  Serial.println("JSON Data:");
  Serial.println(buffer);

  url += apiKey;
  Serial.print("Requesting URL: ");
  Serial.println(url);

  client.print(String("POST ") + url + " HTTP/1.1\r\n" +
               "Host: " + host + "\r\n" +
			         "Connection: close\r\n" +
               "Content-Type: application/json\r\n" +
               "Content-Length: " + measureJson(jsonDoc) + "\r\n\r\n" +
               buffer + "\r\n");
 
  while (client.connected() || client.available()) {
    if (client.available()) {
        String line = client.readStringUntil('\n');
        Serial.println(line);
        if (line.length() > 2) { // IFFT returns a message when it receives a signal
          ifttt_retry = 0;
          client.stop();
          return(1);
        }
      }
  }
  client.stop();

  if (ifttt_retry > 2) {  // Try a maximum of 3 times
    ifttt_retry = 0;
    return(1);
  }
  ifttt_retry++;
  return (0);  // Returning zero will cause this function to be called again
}

void status_leds(bool red, bool green, bool blue, bool blink)
{
  redState   = !red;
  greenState = !green;
  blueState  = !blue;
  blinkState = blink;

  digitalWrite(RED_LED, redState);
  digitalWrite(GREEN_LED, greenState);
  digitalWrite(BLUE_LED, blueState);
}

void blink_leds()
{
  static bool blink_on_off = 0;
  static unsigned long int blinkTimer = millis();

  if (blinkState) {
    if (millis() - blinkTimer > BLINK_PERIOD) {
      blink_on_off = !blink_on_off;
      blinkTimer = millis();

      digitalWrite(RED_LED, blink_on_off || redState);
      digitalWrite(GREEN_LED, blink_on_off || greenState);
      digitalWrite(BLUE_LED, blink_on_off || blueState);
    }
  }
}


void readStandbyButton() {
  static int buttonState = HIGH, lastButtonState = HIGH;
  static long lastDebounceTime = 0;

  int buttonReading = digitalRead(STANDBY);

  if (buttonReading != lastButtonState) {
    lastDebounceTime = millis();  // reset debounce timer
  }

  if ((millis() - lastDebounceTime) > 50) { // Wait 50 msec before reading button

    if (buttonReading != buttonState) {
      buttonState = buttonReading;

      if (buttonState == LOW) {  // Button has been pushed (grounded)
        standbyMode = !standbyMode;  // Toggle standby mode
        standbyModeTime = millis();  // Reset timer
        if (standbyMode) {
          status_leds(0, 0, 1, 1); // Blink blue in standby mode
          Serial.println("Standby Mode");
        }
        else {
          if (digitalRead(DOOR) == CLOSED) {
            status_leds(0, 1, 0, 0); // Door shut, status = Green
          }
          else {
            status_leds(1, 0, 1, 0); // Door open, status = Magenta
            changeTimer = millis();  // Reset 15 minute timer
          }
          Serial.println("Ready Mode");
        }
      }
    }
  }

  if (((millis() - lastDebounceTime) > 5000) && (buttonReading == LOW)) {  // Button has been depressed for 5 seconds
     WiFiManager MyWifiManager;

     MyWifiManager.resetSettings();  // Reset WIFI
     delay(3000);
     ESP.restart();
     delay(5000);
  }
  lastButtonState = buttonReading;
}

void configModeCallback (WiFiManager *myWiFiManager) {
#ifdef OLED_DISPLAY 
  display.clearDisplay();
  display.setCursor(0,0);
  display.println("GARAGE DOOR MONITOR");
  display.println("WIFI SETUP");
  display.println("To configure Wifi,  ");
  display.println("connect to Wifi ");
  display.println("network GARAGE_DOOR");
  display.println("password: PASSWORD");
  display.println("and open 192.168.4.1");
  display.println("in web browser");
  display.display();   
#endif
}

void eepromRead(char *str, int addr, int len) {
  for (int i=0; i<len; i++) {
    str[i] = EEPROM.read(addr+i);
  }
  str[len-1] = '\0'; // Ensures last byte will be null character
}

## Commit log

2016-12-31 Initial commit of code and schematic.
    [gdoor.brd, gdoor.sch]
2017-01-08 Fixed issue with standby button
    [GarageDoorMonitor.ino]
2017-01-21 OpenSCAD and STL files
    Add files for a 3D printed case.
    [GarageDoorMonitorCase.scad, GarageDoorMonitorCase.stl]
2017-02-02 Mounting plate and bottom with standoffs
    The bottom has standoffs positioned to match the screw holes in the
    board.
    Photos included.
    [GarageDoorMonitorBottom.stl, GarageDoorMonitorCase.scad, GarageDoorMonitorCase.stl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]
2017-02-25 Add case for garage door monitor with OLED
    [Button.stl, GarageDoorMonitorBase.stl, GarageDoorMonitorBottom.stl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]
2017-03-29 Accidentally saved the bottom last time under this filename. This is the correct file.
    [GarageDoorMonitorCase.stl]
2017-10-06 Improved button flexibility. Updated instructions.
    [GarageDoorMonitorCaseWithOLED.skp, GarageDoorMonitorCover.stl]
2017-10-25 Update OLED mount
    [GarageDoorMonitorCaseWithOLED.skp, GarageDoorMonitorCover.stl]
2018-11-21 Code and PCB modified for robustness
    [gdoor.brd, gdoor.sch]
2021-09-05 Added OLED Timeout to prevent OLED burn-in. Updated code to work with ArduinoJson v6.
    [GarageDoorMonitor.ino]

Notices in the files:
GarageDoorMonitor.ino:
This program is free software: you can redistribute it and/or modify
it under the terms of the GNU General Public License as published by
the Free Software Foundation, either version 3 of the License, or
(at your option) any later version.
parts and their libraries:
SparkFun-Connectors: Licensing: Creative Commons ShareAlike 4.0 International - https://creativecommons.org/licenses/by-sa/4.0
